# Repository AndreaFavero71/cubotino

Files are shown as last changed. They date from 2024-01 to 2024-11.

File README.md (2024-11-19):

# CUBOTino autonomous

This repo contains the relevant files for ....

How to make CUBOTino autonomous: A small, 3D printed, Rubik's cube solver robot
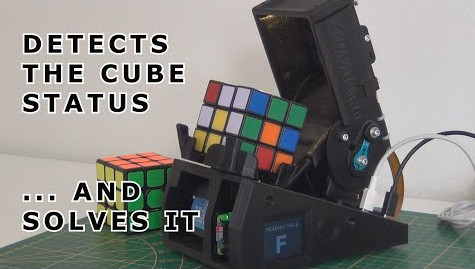
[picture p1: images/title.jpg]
title image


Further robot info at: https://www.instructables.com/CUBOTino-Autonomous-Small-3D-Printed-Rubiks-Cube-R/

An impression of the robot: https://youtu.be/dEOLhvVMcUg and https://youtu.be/YV-g_3STsBo

This is forked from the git repo made by heneault (thank you !!!), and updated to latest files versions.

This git repo simplifies the download of the individual files and automates as much a possible the deployment to the Raspberry Pi

This installation has proved to work on different Raspberry Pi models; Please report in case you experience issues.

# How to use it:
1. Flash your SD card according to the procedure in the [document here](doc/How_to_make_CUBOTino_autonomous_robot_20241119.pdf) , Chapter 7, Step1 to Step3
2. Put the sd card in the pi and power it. You can monitor the boot process if you connect an hdmi monitor to it but it is not essential. 
3. Try to connect to the Raspberry Pi via SSH. On Windows you can use Putty. On linux and mac you can type directly:
```
ssh pi@cubotino.local
```
4. If you can't reach the pi like this, you will have to scan your network to find the IP to use
5. After you are connected via ssh, type the following commands in the shell:
```
git clone https://github.com/AndreaFavero71/cubotino.git
cd cubotino/src
chmod +x install/setup.sh
sudo ./install/setup.sh
```
6. Make sure the script runs without error until the end. It should ask you to reboot. Type 'y' and hit enter.
7. If the question "Reboot (y/n)" does't appear, them the installation is facing issues; Try to fix the errors, and run the script again.
8. If the question "Reboot (y/n) does appear, You should get the proper environment after the reboot.

# Build the robot:
Follow the instructions (saved at /doc folder)

# Tuning the servos position via GUI (via VNC):
```
cd ~/cubotino/src
source .virtualenvs/bin/activate
python Cubotino_T_servos_GUI.py
```
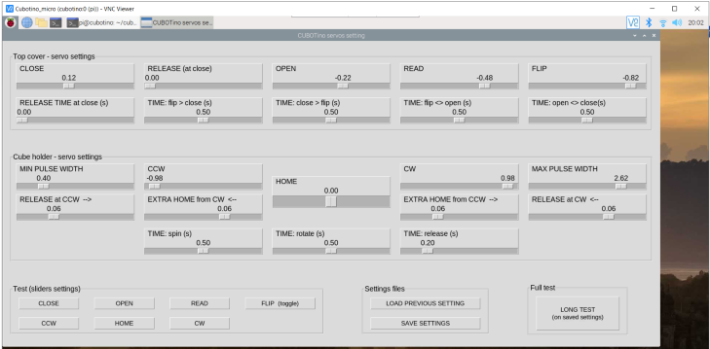
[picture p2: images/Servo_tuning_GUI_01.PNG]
title image


# Executing manually
From a shell, you can run the main python script like this:
```
cd ~/cubotino/src
source .virtualenvs/bin/activate
python Cubotino_T.py
```
of course, you can replace `Cubotino_T.py` by any other python scripts as mentioned in the documentation.

# Enabling autostart
When everything is tuned and you want to autostart the software automatically on reboot, just type :
```
    sudo crontab -e
```
select the nano editor '1' then go to the last line of the window and remove the first '#' character of the line . This uncomment the startup script that launches cubotino on startup. You can reboot after to test it.

# VNC connection
You can always connect with ssh. If you prefere VNC you can download the RealVNC client (this is the one I use). You just have that start it like this:
```
vncviewer cubotino.local
```
It will ask for the credential. Use 'pi' and the same password you use for ssh. You should have a desktop version in this way

Check out the "How_to_make ...  .pdf" document (at /doc folder) for further info.<br /><br />

# Please leave a feedback if you build it
I hope many of you will decide to build your own CUBOTino, and that you'll enjoy it as much much as I did. <br />
I hope you will also post an "I Made it", on the Instructables site of this project (link above); <br />
I can ensure you, seeing a new born CUBOTino makes me feel very well 🙂

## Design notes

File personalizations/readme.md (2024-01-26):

# Personalizations <br />

If you have personalized your Cubotino, and you'd like to share your cad files, SW snippets/file, etc: <br />

- This is the right folder. <br />
- Add a suffix with your name in front of all the files. <br />
- Add a text file, with your name in front :-) , to briefly explain what is about; If needed please add guidance for others. <br />
- Add a picture, with your name in front :-) , in case the personalization is mainly aesthetic. <br />
- Submit your pull request. <br />

Thank you <br />
Andrea <br />

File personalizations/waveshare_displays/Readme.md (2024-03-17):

# Waveshare 1.8 and 2 inch displays

- Both are fully compatable with the current version of cubotino.
- The [Waveshare 1.8inch](https://www.waveshare.com/product/displays/lcd-oled/lcd-oled-3/1.8inch-lcd-module.htm) display is a 160x128 ST7735 based display.
- The [Waveshare 2.0inch](https://www.waveshare.com/product/displays/lcd-oled/lcd-oled-3/2inch-lcd-module.htm) display is a 320x240 ST7789 based display.
- The STL files to print are attached for the USB-C Power input variants.
- The 1.8in display mounts to the PCB_Cover with 2.5mm screws, They are included with the screen
- The 2in display  mounts to the PCB_Cover with 2.0mm screws, They are included with the screen

# Wiring
- The connector on the back of the display is a [JST PH](https://www.jst.com/products/crimp-style-connectors-wire-to-board-type/ph-connector/) series connector.
- These displays come with a cable to connect the display to your PCB. Or they can be soldered. The cable provided has 
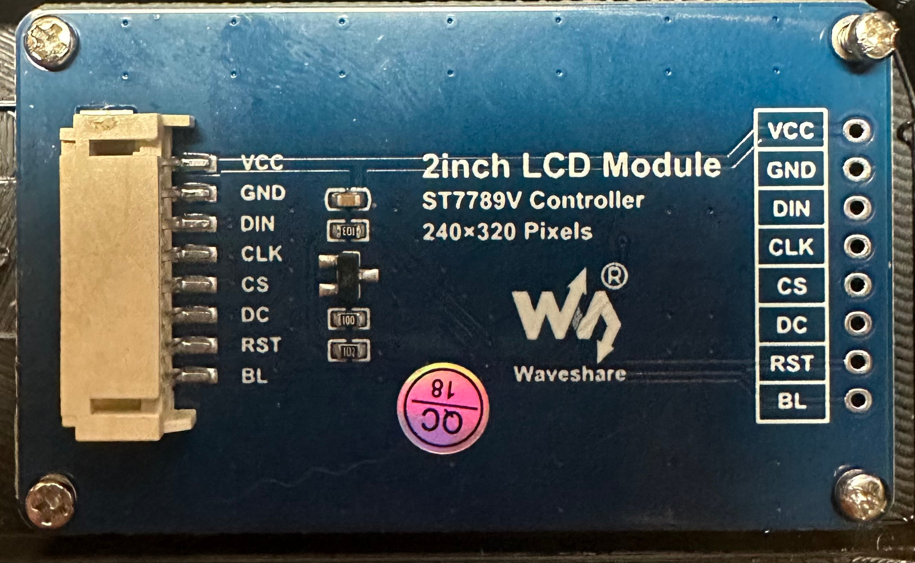
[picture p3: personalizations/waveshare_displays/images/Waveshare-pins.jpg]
Wire Diagram
individual leads with dupont connectors. 
- Using the [Cubotino Schematic](/connections_board/info/Schematic_Cubotino.pdf), the table below is used to connect the wires.

| Connections PCB Pin order | PCB Pin name | Waveshare Pin name | Waveshare Pin order |
|---|---|---|---|
| 1 | GND | GND | 2 |
| 2 | +3.3 | VCC | 1 |
| 3 | SCLK | CLK | 4 |
| 4 | MOSI | DIN | 3 |
| 5 | GP22 | RST | 7 |
| 6 | GP27 | DC | 6 |
| 7 | CS0 | CS | 5 |
| 8 | GP4 | BL | 8 |

# Assembly
- Here is a couple of pictures of my assembly.  Note: While I used a custom PCB. It is based on the [PCB Schematic](/connections_board/info/Schematic_Cubotino.pdf) in this project.
- There is about 20mm between the connections pCP and the Display.
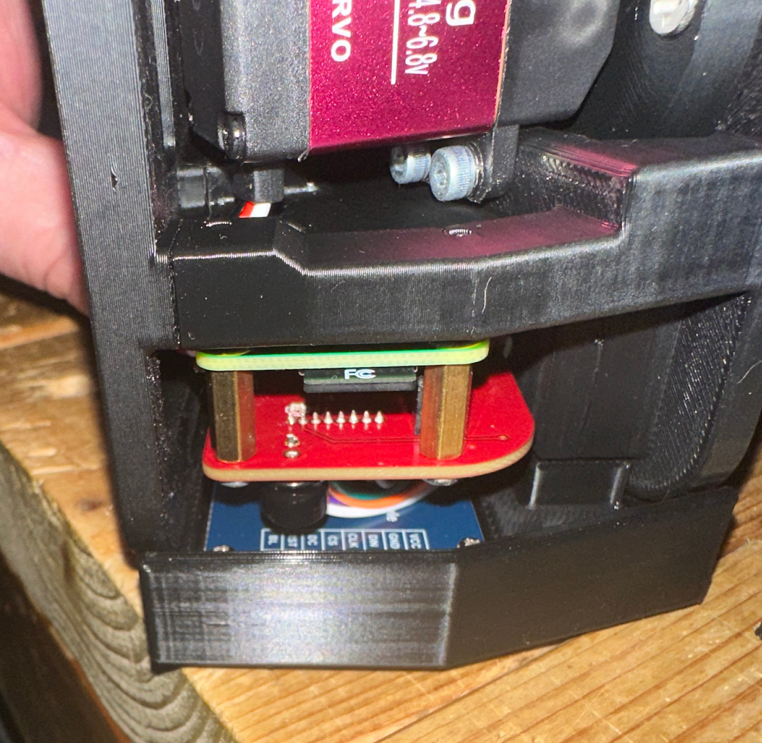
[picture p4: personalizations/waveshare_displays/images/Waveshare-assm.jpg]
Assembly

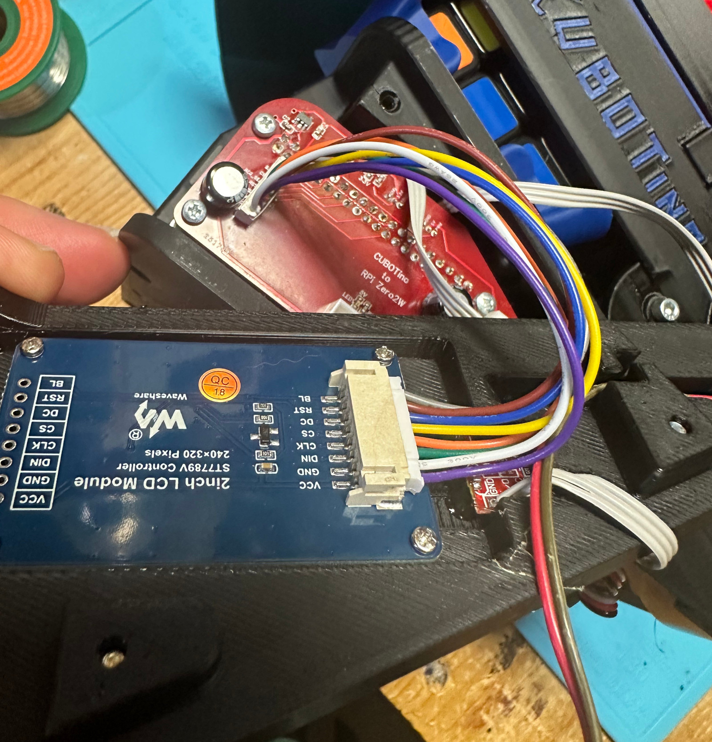
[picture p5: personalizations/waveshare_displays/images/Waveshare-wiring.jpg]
Wiring


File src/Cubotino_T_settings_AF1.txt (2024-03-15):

{
"frameless_cube": "auto",
"disp_type": "st7735",
"disp_width": "130",
"disp_height": "162",
"disp_offsetL": "-2",
"disp_offsetT": "-2",
"disp_flip": "false",
"camera_width_res": "640",
"camera_hight_res": "480",
"s_mode": "7",
"kl": "0.95",
"x_l": "70",
"x_r": "60",
"y_u": "20",
"y_b": "95",
"warp_fraction": "7",
"warp_slicing": "1.5",
"square_ratio": "1",
"rhombus_ratio": "0.3",
"delta_area_limit": "0.7",
"sv_max_moves": "20",
"sv_max_time": "2",
"collage_w": "1024",
"marg_coef": "0.06",
"cam_led_bright": "0.1",
"detect_timeout": "40",
"show_time": "7",
"warn_time": "1.5",
"quit_time": "3.5",
"cover_self_close": "true",
"vnc_delay": "0.0",
"built_by": "",
"built_by_x": "25",
"built_by_fs": "16",
"fcs_delay": "3"
}

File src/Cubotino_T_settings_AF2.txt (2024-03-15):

{
"frameless_cube": "auto",
"disp_type": "st7735",
"disp_width": "128",
"disp_height": "164",
"disp_offsetL": "0",
"disp_offsetT": "-4",
"disp_flip": "false",
"camera_width_res": "640",
"camera_hight_res": "480",
"s_mode": "7",
"kl": "0.95",
"x_l": "56",
"x_r": "106",
"y_u": "48",
"y_b": "100",
"warp_fraction": "7.2",
"warp_slicing": "1.5",
"square_ratio": "1.0",
"rhombus_ratio": "0.3",
"delta_area_limit": "0.7",
"sv_max_moves": "20",
"sv_max_time": "2.0",
"collage_w": "1024",
"marg_coef": "0.06",
"cam_led_bright": "0.04",
"detect_timeout": "40",
"show_time": "7",
"warn_time": "1.5",
"quit_time": "3.5",
"cover_self_close": "True",
"vnc_delay": "0.5",
"built_by": "",
"built_by_x": "25",
"built_by_fs": "16",
"expo_shift": "-0.2",
"fcs_delay": "3.0"
}

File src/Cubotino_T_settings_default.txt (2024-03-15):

{
"frameless_cube": "false",
"disp_type": "st7735",
"disp_width": "128",
"disp_height": "160",
"disp_offsetL": "0",
"disp_offsetT": "0",
"disp_flip": "false",
"camera_width_res": "640",
"camera_hight_res": "480",
"s_mode": "7",
"kl": "0.95",
"x_l": "0",
"x_r": "0",
"y_u": "0",
"y_b": "0",
"warp_fraction": "7",
"warp_slicing": "1.5",
"square_ratio": "1",
"rhombus_ratio": "0.3",
"delta_area_limit": "0.7",
"sv_max_moves": "20",
"sv_max_time": "2",
"collage_w": "1024",
"marg_coef": "0.1",
"cam_led_bright": "0.1",
"detect_timeout": "40",
"show_time": "7",
"warn_time": "1.5",
"quit_time": "3.5",
"cover_self_close": "false",
"vnc_delay": "0.0",
"built_by": "",
"built_by_x": "25",
"built_by_fs": "16",
"expo_shift": "-0.6",
"fcs_delay": "3"
}

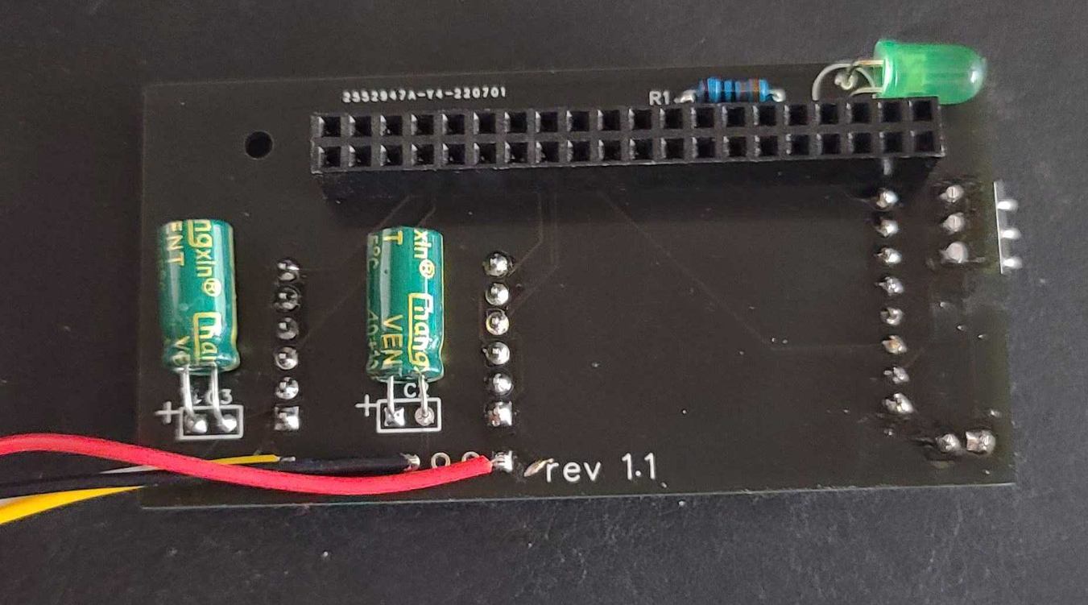
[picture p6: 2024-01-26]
connections_board/info/Cubotino_Rev_1.1_Back_View.jpg

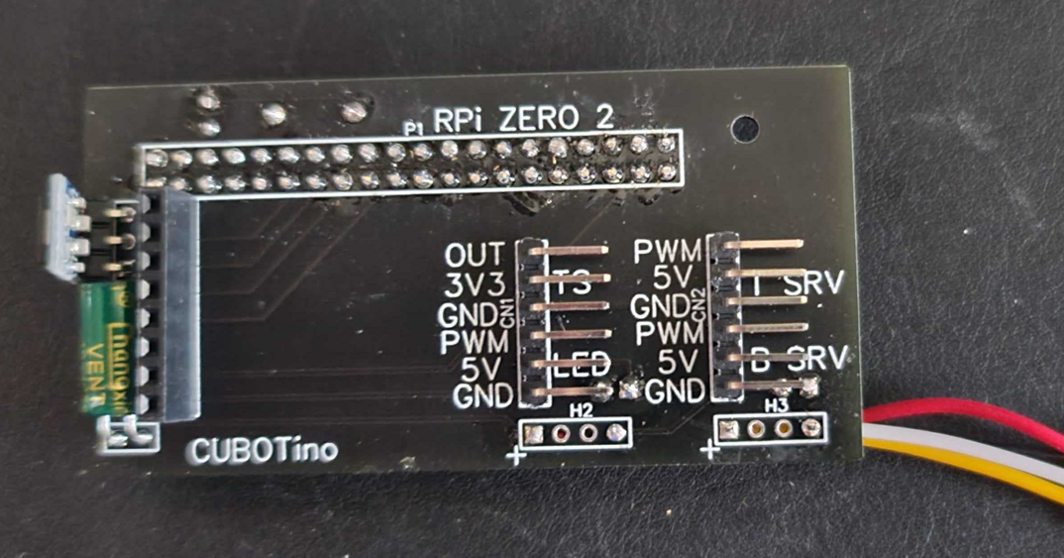
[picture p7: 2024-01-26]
connections_board/info/Cubotino_Rev_1.1_Front_View.jpg

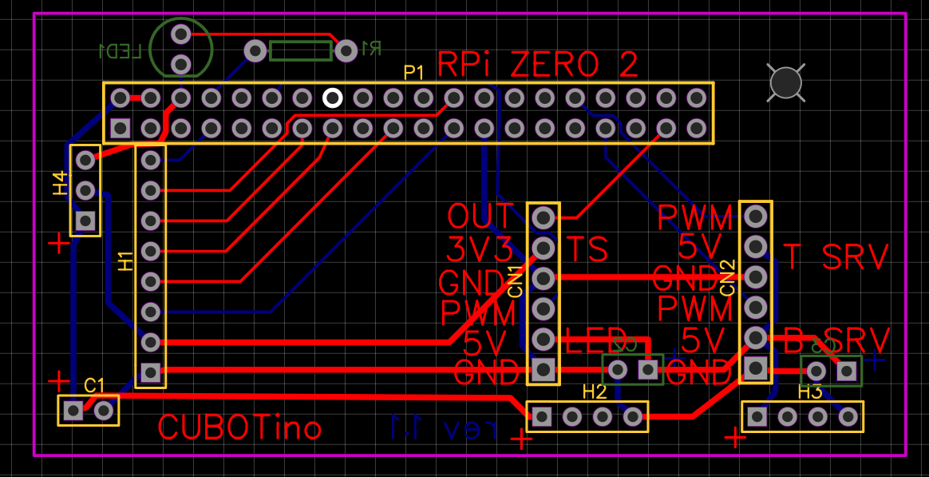
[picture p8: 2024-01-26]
connections_board/info/Cubotino_PCB_Rev-1.1.png

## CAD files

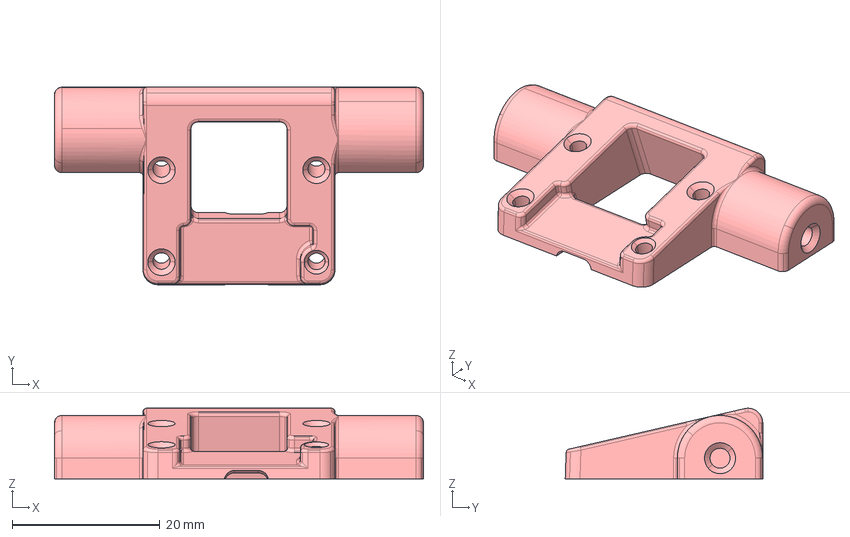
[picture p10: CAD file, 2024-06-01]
stp/PiCamera_holder_V1_V2_V3.stp
50.0 x 26.8 x 9.57 mm

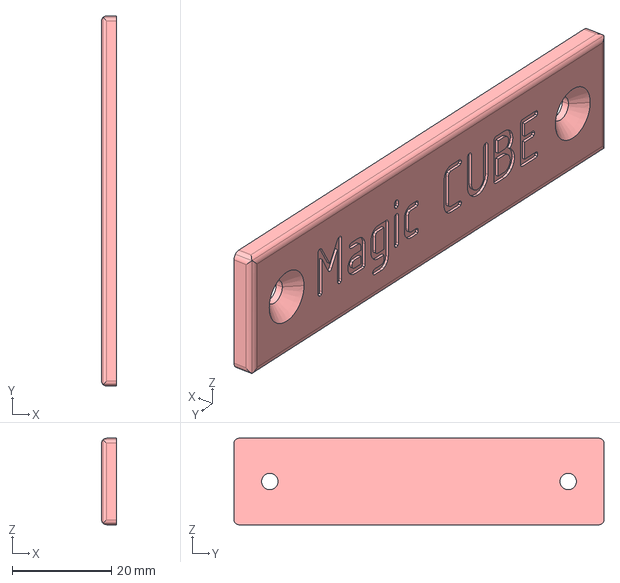
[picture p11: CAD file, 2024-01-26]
stp/Personaliz_plate_01.stp
3.00 x 74.4 x 17.4 mm

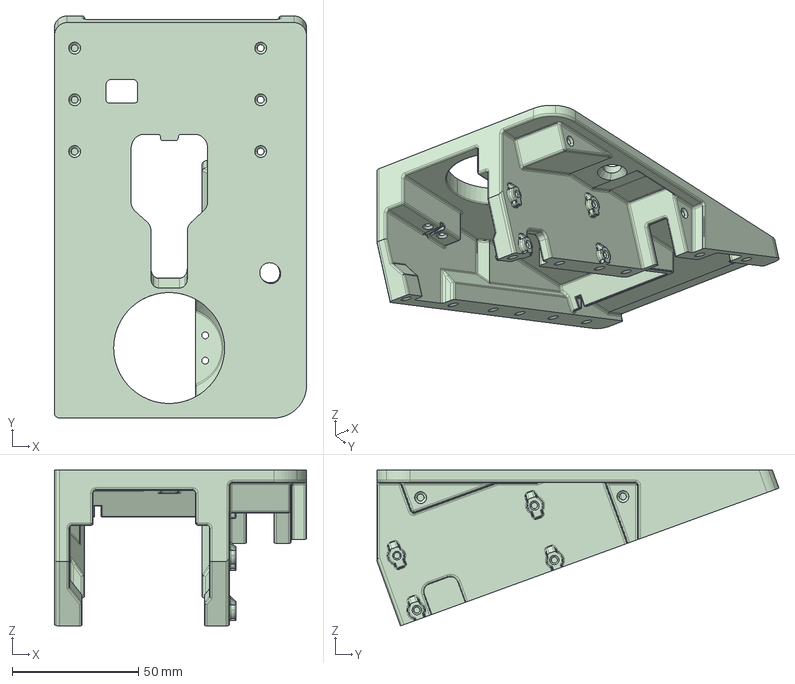
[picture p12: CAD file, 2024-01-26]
stp/Structure.stp
100.0 x 159.4 x 61.8 mm

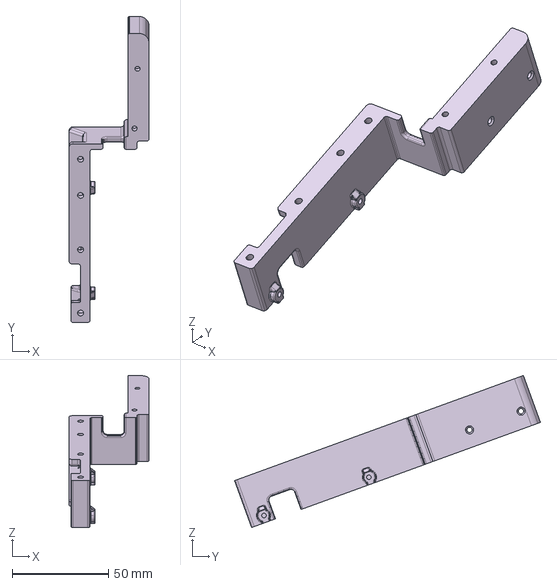
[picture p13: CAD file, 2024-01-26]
stp/Extension_middle.stp
41.5 x 158.9 x 79.0 mm

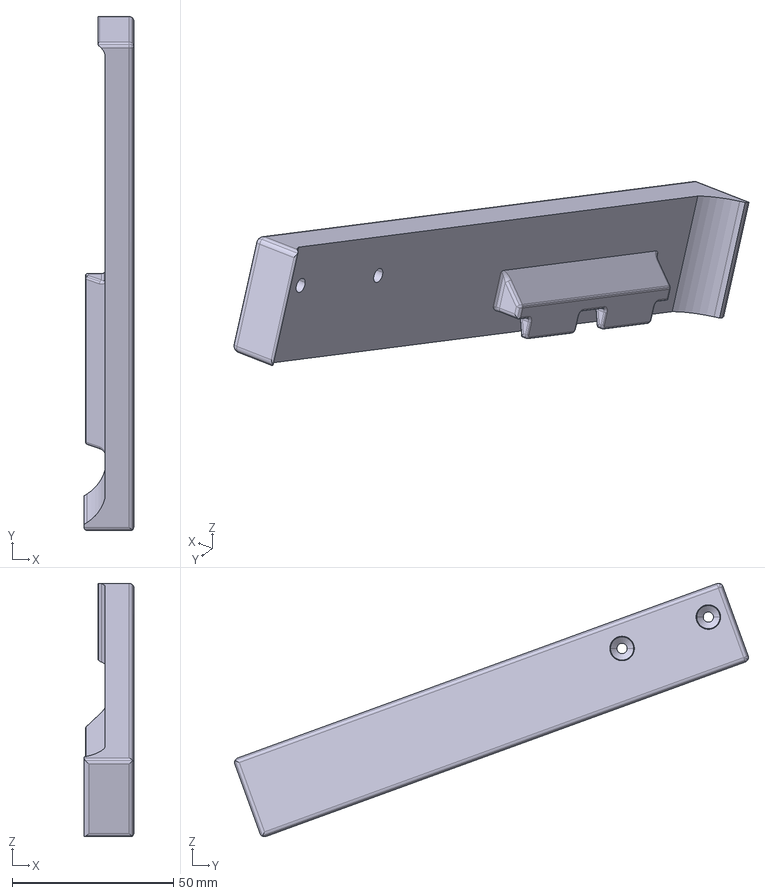
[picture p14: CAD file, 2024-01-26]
stp/Extension_right.stp
15.5 x 159.3 x 78.5 mm

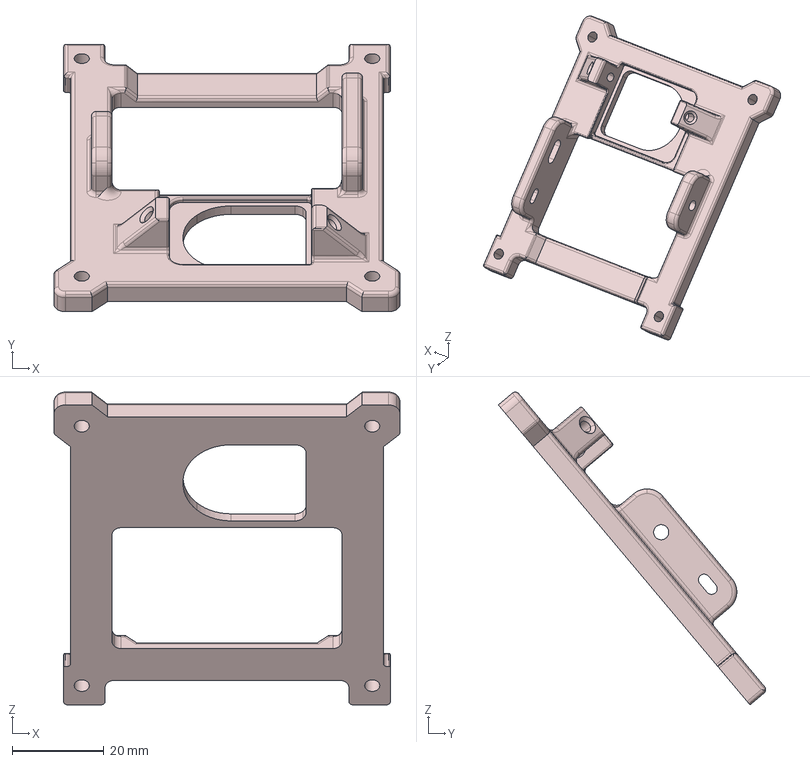
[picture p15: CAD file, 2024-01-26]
stp/Picamera_holder_frame.stp
75.5 x 58.4 x 68.3 mm

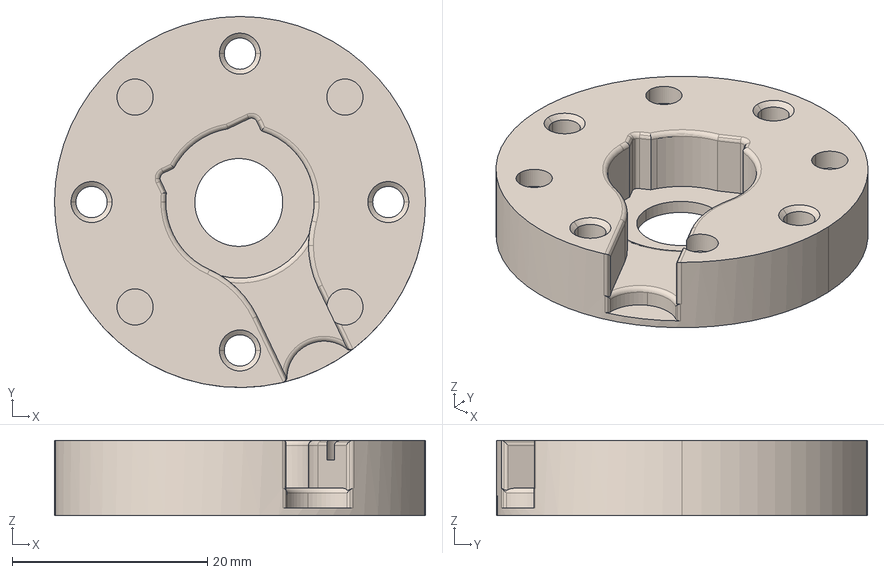
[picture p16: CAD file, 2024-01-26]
stp/Alternative_Servo_axis_inf.stp
38.0 x 38.0 x 7.70 mm

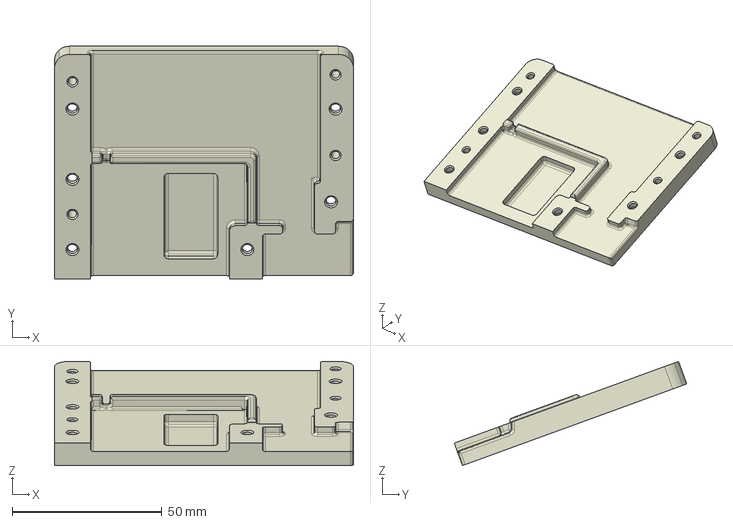
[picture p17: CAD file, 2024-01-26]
stp/Baseplate_rear.stp
100.0 x 77.8 x 34.8 mm

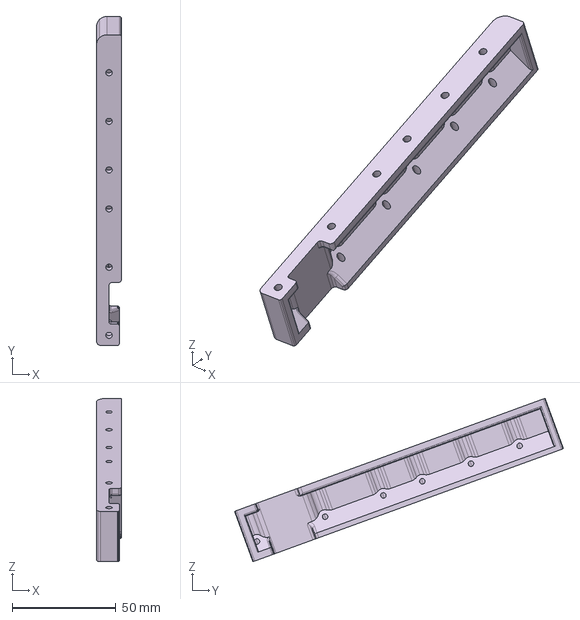
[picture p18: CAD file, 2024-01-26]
stp/Extension_left.stp
12.0 x 158.9 x 79.0 mm

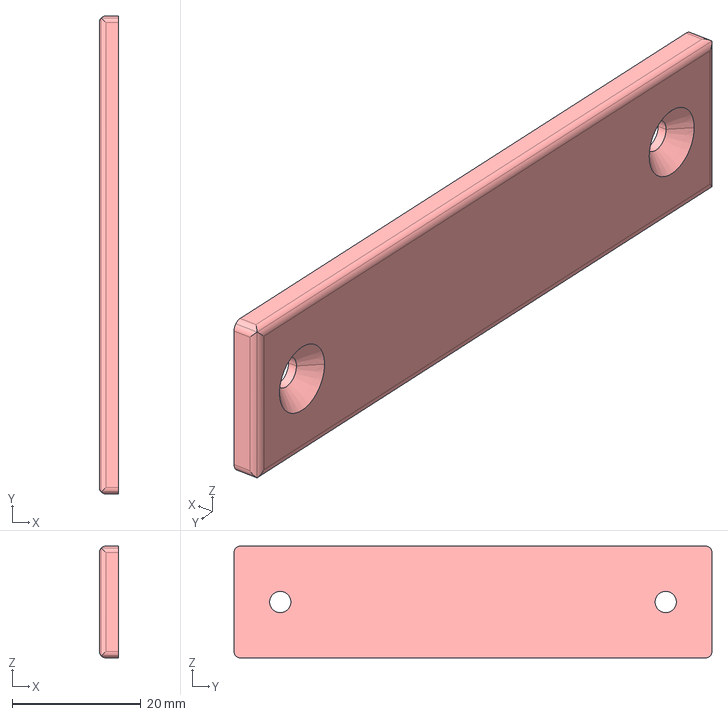
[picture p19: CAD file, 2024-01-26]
stp/Personaliz_plate.stp
3.00 x 74.4 x 17.4 mm

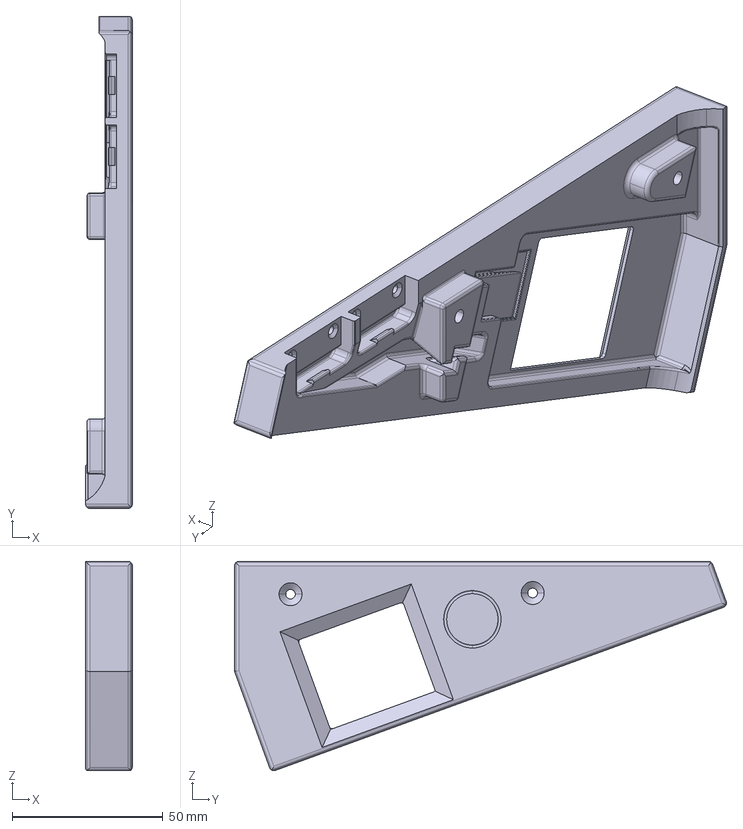
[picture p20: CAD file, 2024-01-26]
stp/PCB_cover_display.stp
15.5 x 163.0 x 69.4 mm

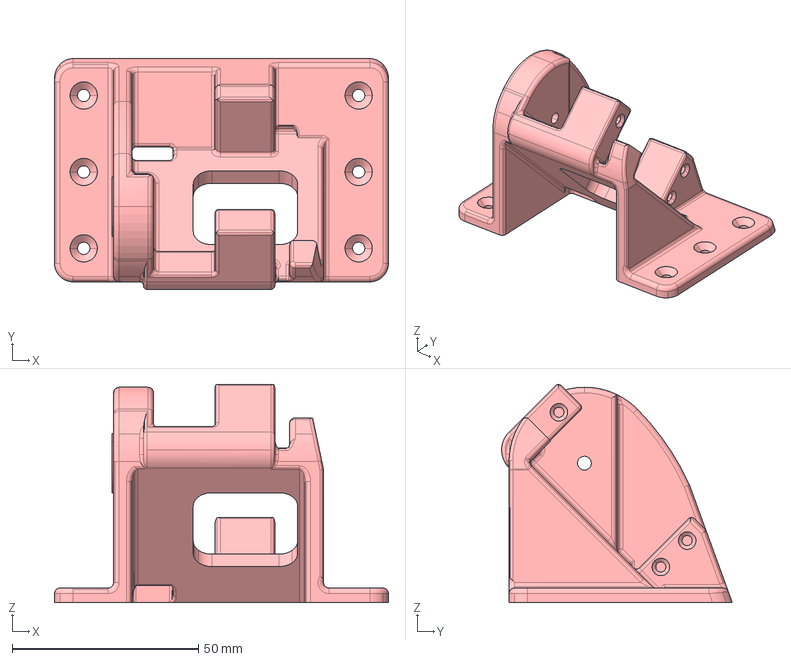
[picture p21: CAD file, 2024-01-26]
stp/Hinge.stp
89.6 x 61.9 x 58.6 mm

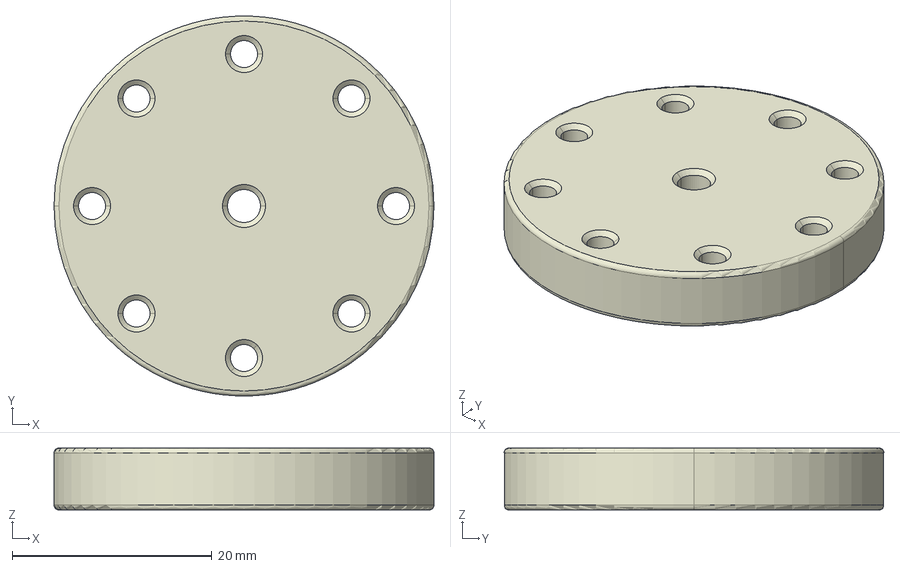
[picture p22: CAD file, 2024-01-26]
stp/Alternative_Servo_axis_sup.stp
38.0 x 38.0 x 6.20 mm

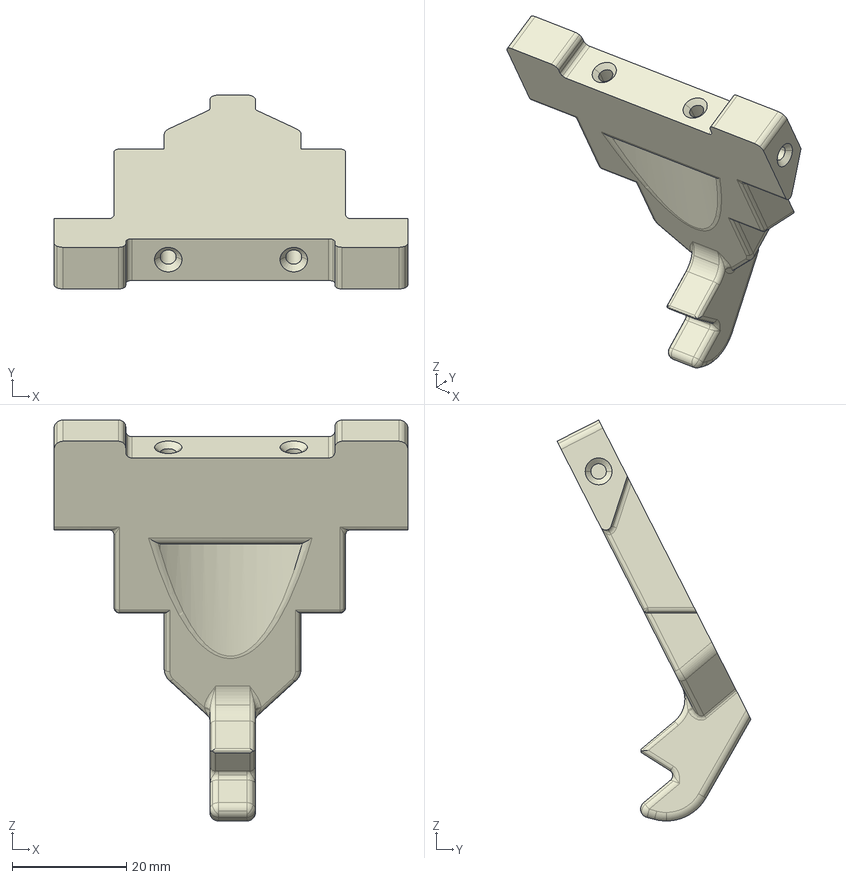
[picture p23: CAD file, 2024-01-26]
stp/Lifter.stp
62.0 x 34.0 x 70.3 mm

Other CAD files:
stp/Servo_axis_inf.stp
stp/Baseplate_front.stp
stp/Servo_axis_sup.stp
stp/Top_cover.stp
stl/Alternative_Servo_axis_inf.stl
stl/Alternative_Servo_axis_sup.stl
stl/Baseplate_rear.stl
stl/Extension_left.stl
stl/Extension_middle.stl
stl/Extension_right.stl
stl/Lifter.stl
stl/Personaliz_plate.stl
stl/Personaliz_plate_01.stl
stl/PiCamera_holder_V1_V2_V3.stl
stl/Servo_axis_inf.stl
stl/Servo_axis_sup.stl
stp/PCB_cover_display_UsbC.stp

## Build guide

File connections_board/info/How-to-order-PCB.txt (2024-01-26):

How to Order PCB

Please refer to:
https://docs.easyeda.com/en/PCB/Order-PCB

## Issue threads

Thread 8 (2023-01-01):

Schematic for the PCB

belenhed, 2023-01-01:
Hello can we have the schematic for the PCB so maybe we can make one at home with a CNC?
Thanks

AndreaFavero71, 2023-10-15:
This answer is absolutely late.....anyhow:
https://github.com/AndreaFavero71/cubotino/blob/main/connections_board/info/Schematic_Cubotino.pdf

AndreaFavero71, 2023-10-15:
Schematic is finally loaded

Closed 2023-10-15.

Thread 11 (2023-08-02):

Errors in RPi setup

MasterMD, 2023-08-02:
Hi!
Great project !!
During the execution of the setup.sh I got an error :
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
but the procedure continues.
But at about 47% of the unpacking it stops with this error:
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
I repeated the whole procedure (from writing new image on the SD card), but same result.
What to do?

kind regards,
Maarten

AndreaFavero71, 2023-08-06:
Hi, I'm going to be holiday for one more week and I'm not equipped to run any test.
In case there are recent changes on libraries, blocking the installation, there is little I can do shortly.

What I can do now, is to double check with you if any error at your side.
On 15th July 2023 the installation process was working fine: If you share your email address I'll send you the printout log I've saved (and downloaded from my NAS).
Are you sure the flashed OS is the "Raspberry Pi OS (Legacy)”, not the default one proposed by the Raspberry Pi Imager?
If the chosen OS is correct, which Raspberry Pi board are you using?

Kind regards
Andrea

MasterMD, 2023-08-06:
Hi Andrea,

Thanks for your response!

After my experience with the RPi installation part, I was a little confused what to do.
(burning the image and verifying had been succesfull)

A few days later I decided to try it again with a different SD card, and ... the procedure finished succesfull !!
Sorry, that I didn't update my GitHub thread yet ...

I went on with the assembly, and 'discovered' that my camera extension flat cable was of a wrong type
(some years ago I build a cube resolver with RPi 3 and Technic Lego construction, so I thought I have a camera and cable ;-)
but I wasn't aware that the Zero has a different connection).

I ordered a new cable, and started testing. Unfortunately the camera didn't function (at all).
The connection at the Pi Zero appears to be rather fragile, but after re-arranging the camera still doesn't work.
Now I am awaiting a new camera board; hopely I can proceed then.

I admire the way you have set-up this whole project: the lovely design, and surely the extended documentation.
I found some details to (maybe) improve. I you like it, I will send them as soon as I have my Cubotino operating.

Thanks again !

Kind regards,
Maarten

AndreaFavero71, 2023-08-06:
Hi Maarten, very good you found the solution for the setup issue.
I'll close this thread with a comment about microSD and possible setup
errors, and I'll add it to the troubleshooting chapter.

I received once a bad camera cable: At the CSI connector extremity, the
insulation was too large at one side (and narrow al the opposite side)
preventing the traces alignment (connection) to the CSI connector.
I did cut away a narrow strip of insulation, and inserted the cable forced
to that side: That arrangement is still working after one year, including a
few reopening of it.

I'm always open for corrections and improvements; Please collect and share
them via email, to ***@***.***, once you'll have your bot up
and running.

Kind regards
Andrea

Il dom 6 ago 2023, 12:16 MasterMD ***@***.***> ha scritto:

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

AndreaFavero71, 2023-08-14:
In case of Errors in Rpi setup, try with a different microSD as it might be the source of the problem

Closed 2023-08-14.

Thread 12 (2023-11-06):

CPL file for JLCPCB board assembly

KH6JAG, 2023-11-06:
Is there a CPL file available to request a quote from JLCPCB for board and assembly?
The link given in connections_board/info/ is only for the board.

When chatting with JLCPCB today, I was advised that I need to either provide the CPL file or do a complete design using EadyEDA.
The Gerber files imported without error to do a board order, but they cannot be imported into Easy EDA.

I've also asked PCBWAY for a quote on the assembled board - they usually respond in 2-3 days with a quote for assembled boards.

Thanks for all your Cubotino project efforts!

AndreaFavero71, 2023-11-06:
Hi, I just googled what CPL file is meant for, and it looks like it includes the BOM (all compoents), as per the issue title you have raised :-)
I'm afraid I don't have the CPL file, the board has been drawn by another Maker and the files I received are those that are published.
I hope you'll take a big breath, and decide to order/solder the components by yourself...
Regards, Andrea

KH6JAG, 2023-11-07:
<!--
/* Font Definitions */
@font-face
	{font-family:"Cambria Math";
	panose-1:2 4 5 3 5 4 6 3 2 4;}
@font-face
	{font-family:Calibri;
	panose-1:2 15 5 2 2 2 4 3 2 4;}
@font-face
	{font-family:"Malgun Gothic";
	panose-1:2 11 5 3 2 0 0 2 0 4;}
@font-face
	***@***.*** Gothic";}
/* Style Definitions */
p.MsoNormal, li.MsoNormal, div.MsoNormal
	{margin:0in;
	font-size:11.0pt;
	font-family:"Calibri",sans-serif;}
a:link, span.MsoHyperlink
	{mso-style-priority:99;
	color:blue;
	text-decoration:underline;}
.MsoChpDefault
	{mso-style-type:export-only;}
@page WordSection1
	{size:8.5in 11.0in;
	margin:1.0in 1.0in 1.0in 1.0in;}
div.WordSection1
	{page:WordSection1;}
-->Thanks for the reply.  I think I can build the CPL file from the info provided by the board maker on the PCBWAY share site.The JLCPCB site offered a potential lower cost source of supplyI have already have soldered a breadboard unit from the Instructable.The newer build is to support a group of youngsters so they wouldn’t need to solder as in requires SMD and just do a mechanical build.Thanks again,  Jim Sent from Mail for Windows From: AndreaSent: Monday, November 6, 2023 1:37 PMTo: AndreaFavero71/cubotinoCc: KH6JAG; AuthorSubject: Re: [AndreaFavero71/cubotino] CPL file for JLCPCB board assembly (Issue #12) Hi, I just googled what CPL file is meant for, and it looks like it includes the BOM (all compoents), as per the issue title you have raised :-)I'm afraid I don't have the CPL file, the board has been drawn by another Maker and the files I received are those that are published.I hope you'll take a big breath, and decide to order/solder the components by yourself...Regards, Andrea—Reply to this email directly, view it on GitHub, or unsubscribe.You are receiving this because you authored the thread.Message ID: ***@***.***> 

AndreaFavero71, 2023-11-08:
Hi Jim,
I've the feeling you are referring to the the board designed by G2G, as you're mentioning smd components.
This board, despite having some positive aspects, is not supported by me and not described in the instructions. In my opinion, this board increases complexity by adding extra connectors (i.e on the display) and smd components.
If you prefer this board, as it comes fully assembled, please note you'll have to use specific connectors at the servos, led module,  touch sensor and display: For reference, please check the "I MADE IT" made by g2maurer at Instructables (https://www.instructables.com/CUBOTino-Autonomous-Small-3D-Printed-Rubiks-Cube-R/#discuss).
g2maurer has posted the email in case there are maker interested on getting that board: Please check the chat at Instructables page for his/her email address.
You'll also notice the display is screwed directly to the PCB_cover, therefore you'll better ask g2maurer for the stl file.

For the supported board (V1.6) the gerber files are saved at /gerber folder on this project; This board is "just" essential, no BOM saved at the boards manufacturer, yet it only uses little through hole components.
This board is the one described in the instructions.

I'm ok with both option, yet it's important you're aware about the differences.
I hope you and the youngsters will have fun with the project.
Regards, Andrea

AndreaFavero71, 2023-11-11:
This issue relates to a board version that isn't supported by Andrea Favero, board not covered in the instructions.
The supported board (V1.6) doesn't have smd components, neither the CPL file yet is is simple to solder at home.

KH6JAG, 2023-11-11:
Thank you for the reply.  We have a project that is building as many of the Rubik's robots that have good documentation.  Cubotino has one of the best documentation sets.  I was able to get a build quote for the boards that required the CPL file.  I'll send you an update once the units are built with these boards.

Closed 2023-11-11.

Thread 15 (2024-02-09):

Display test not working and install doesnt work properly.

varkanoid, 2024-02-09:
Hi,

I decided to change my microsd card before I ran through the setup process and tuning. I also saw you had updated recently so I thought I will refresh the whole thing. I had only done a few things before like test the display was working with your test script which it was. I started from scratch and imaged the new micro sd. I then cloned your repository and followed your install instructions.

Issue 1 was when you click y to restart, you get no GUI after the restart. I had to enable it myself with raspi-config.
Issue 2 now when I run the display test I get these errors below. This is strange because with the previous install it worked fine.

(.virtualenvs) pi@cubotino:~/cubotino/src $ python Cubotino_T_display.py
Activated pigpiod
Error on converting imported parameters to int
Display test for 20 seconds
Display shows rectangles, text and Cubotino logo
Traceback (most recent call last):
  File "/home/pi/cubotino/src/Cubotino_T_display.py", line 298, in <module>
    display.test1_display()
  File "/home/pi/cubotino/src/Cubotino_T_display.py", line 217, in test1_display
    w = self.disp_w                                            # display width, retrieved by display setting
AttributeError: 'Display' object has no attribute 'disp_w'

So I am using the one dated 22nd January 2024.

Any ideas ?

varkanoid, 2024-02-09:
Also getting this error when I try to run the Tuning GUI.
(.virtualenvs) pi@cubotino:~/cubotino/src $ python Cubotino_T_servos_GUI.py

Activated pigpiod
Error on converting imported parameters to int
Traceback (most recent call last):
  File "/home/pi/cubotino/src/Cubotino_T_servos_GUI.py", line 30, in <module>
    import Cubotino_T_servos as servo    # custom library controlling Cubotino servos and led module
  File "/home/pi/cubotino/src/Cubotino_T_servos.py", line 37, in <module>
    s_disp.set_backlight(0)     # display backlight is set off
  File "/home/pi/cubotino/src/Cubotino_T_display.py", line 85, in set_backlight
    self.disp.set_backlight(value)
AttributeError: 'Display' object has no attribute 'disp'

varkanoid, 2024-02-09:
Seems some kind of issue with setting the display ?

(.virtualenvs) pi@cubotino:~/cubotino/src $ python Cubotino_T_servos.py -set 0

Activated pigpiod
Error on converting imported parameters to int
Traceback (most recent call last):
  File "/home/pi/cubotino/src/Cubotino_T_servos.py", line 37, in <module>
    s_disp.set_backlight(0)     # display backlight is set off
  File "/home/pi/cubotino/src/Cubotino_T_display.py", line 85, in set_backlight
    self.disp.set_backlight(value)
AttributeError: 'Display' object has no attribute 'disp'

AndreaFavero71, 2024-02-09:
Hi varkanoid,
you are right, I copied the wrong Cubotino_T_settings.txt file.
The settings from this file are uploaded by different scripts.
I have set a system from flashing the image onward: It looks ok now.
Please feedback if it works at your end too.
Regards, Andrea

varkanoid, 2024-02-09:
Works again now than you very much it is appreciated. :)

Just a small thing you left the displ width at 130 instead of the default 128. I know you changed it to 130 for your screen but it works fine with 128 with my screen. Just a minor thing you should be aware of.

AndreaFavero71, 2024-02-09:
Hi, thank you for the note ... just checked that 130 is into the file and instruction since June 2022. I'm going to correct the file now, and the instruction for the next revision.
Wrt the 1st issue you pointed out, after the installation, the Desktop environment can be activated by editing crontab: This is the way I've indicated in the instructions, dor sure there are other ways.
I'm going to close this Issue.
Enjoy the project, Andrea

Closed 2024-02-09.

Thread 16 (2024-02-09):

Error when Cubotino_T_coordinates.txt is missing (or empty)

varkanoid, 2024-02-09:
Hi,

sorry found another issue.

I have done my tuning succesfully. Came to start the solver and it errors below

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

varkanoid, 2024-02-09:
Seems to be this bit in the file it fails on as the .txt file doesnt exist it doesnt define the lines parameter.
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

varkanoid, 2024-02-09:
So I added a blank Cubotino_T_coordinates.txt file and it passed that section with an error.
However I now get this error.
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

AndreaFavero71, 2024-02-10:
Hi Varkanoid, you're right again.
Released an improved version.
Regards, Andrea

varkanoid, 2024-02-10:
Thanks its working now.

varkanoid, 2024-02-10:
Working once again great job. Solved my first cube :)

Closed 2024-02-10.

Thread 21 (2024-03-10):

servos_setting_GUI.py file is required?

AgnesBarta, 2024-03-10:
Hi,

This project sounds really great, we are trying to bring up the source code. We have some issue to init the GUI to do the fine tuning setup. When we are running Cubotino_T_servos_GUI.py it is expecting DISPLAY env variable to be set what is not the case for us. In the latest documentation we see to bring up the GUI with servos_setting_GUI.py but that one I am not able to see in the repo. Could you please help us if we miss something? Thank you so much.

AndreaFavero71, 2024-03-10:
Hi, the GUI file is named Cubotino_T_servos_GUI.py and it requires the virtual environment.
Anyhow, please be informed that today I have released a rather large update (V7.0), involving 7 python files and 2 text files.
Please check, and report, the version of the Cubotino_T.py (add the argument -v , again after activating the virtual enviroment) that gives you the problem.

AgnesBarta, 2024-03-10:
Thank you for confirming. Finally we got the issue resolved and were able to bring the GUI app. Thank you for the quick answer.

AndreaFavero71, 2024-03-10:
Very good. Still applies that I have released an update today, and you might benefit from starting with it.
If of your interest, below the necessary command:
```
git reset --hard origin/main
git pull
```

Closed 2024-03-11.

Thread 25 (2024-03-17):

Settings files getting corrupted when saving from GUI

paul-1, 2024-03-17:
I'm using the GUI to tune my servos.  When saving from the GUI, I'm seeing values getting written wrong, and sometimes after writing, the file is no longer able to be read, as the json has a corrupt format.  I believe it is because of conflicting open calls like this.

https://github.com/AndreaFavero71/cubotino/blob/e5fcf2e7af7ece9f6fb719ae576c74a5f2e58baa/src/Cubotino_T_settings_manager.py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

This is mixing python native file operations with low level os file routines.  I'm not even sure how its working, but they are not compatible.  I would recommend you just use the python open() commands.  Those work with the context manager that you are using.

AndreaFavero71, 2024-03-18:
Hi Paul, I need to check for this.
I've never had problem with this approach. Differently, I had rights issue at the time those two files were cloned from the remote repository, and the robot attempting to write on those.

paul-1, 2024-03-18:
It does not happen every time.  It feels like there are multiple writes to the same file going on.  One common result is the closing } getting repeated twice.   I also saw values that were in the GUI as 3.1 getting written as “3”

Sent from my iPhone

On Mar 18, 2024, at 1:30 PM, Andrea ***@***.***> wrote:

Hi Paul, I need to check for this.
I've never had problem with this approach. Differently, I had rights issue at the time those two files were cloned from the remote repository, and the robot attempting to write on those.

—
Reply to this email directly, view it on GitHub<https://github.com/AndreaFavero71/cubotino/issues/25#issuecomment-2004529060>, or unsubscribe<https://github.com/notifications/unsubscribe-auth/ABRMN4LEKLBGYVCZCHKDBN3YY4QELAVCNFSM6AAAAABE2NAHXKVHI2DSMVQWIX3LMV43OSLTON2WKQ3PNVWWK3TUHMZDAMBUGUZDSMBWGA>.
You are receiving this because you authored the thread.Message ID: ***@***.***>

AndreaFavero71, 2024-03-18:
Ah, then I know: It happens when writing on the same file with less characters than the initial file: The old } remains right after the new inserted one.

After each
```
f.write(json.dumps(whaterver_filename, indent=0))
```
Please add
```
f.truncate()
```
I'll test at my side, please give it a test at yours :-)

AndreaFavero71, 2024-03-18:
Hi Paul,
the settings are saved in the Json files as string
The settings reppresenting values are converted, to integers or to floats, when imported by the Cubotino_T_settings.manager.py
In don't have an explanation about value 3.1 at GUI and "3" at the Json file, but the other way around is possible: Most of the sliders have steps larger than 0.01 (i.e. 0.02) while some default settings are for instance at 0.33 (legacy from before the GUI time).

For the issue you have raise, double } }, it can be reproduced sistematically:
- Set HOME to 0.12 and save. The Json file ends with one }
- Set HOME to 0.0 and save. The Json file ends with two }, as this time less characters were saved while some old ones remained at the file end.

I'm going to commit a fix.

paul-1, 2024-03-18:
Okay, the update seems to fix the bad json, so now the files are getting written properly.  I should could not remember which slider was wrong when I responded today (I was at work)

But the error is in 'warp_slicing' and the problem is reading the slider as an int.
https://github.com/AndreaFavero71/cubotino/blob/bce2f8f3f826e9d64b74439d2aa6d9244493a5a6/src/Cubotino_T_servos_GUI.py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

AndreaFavero71, 2024-03-19:
Hi paul, you're sharp and right.
The warp_slicing parameter is meant to be a float while the slider in takes as integer; This mistake is there since day one of the GUI, 18th April 2023.
This error isn't critic, I'll push the correction once something else will require a commit.

AndreaFavero71, 2024-04-01:
Correction is applied b01a6ec56089ce0dfbc9d7d62913982ef89324f2

Closed 2024-04-01.

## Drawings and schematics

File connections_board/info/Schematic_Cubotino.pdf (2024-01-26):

## USB-C RECEPTABLE

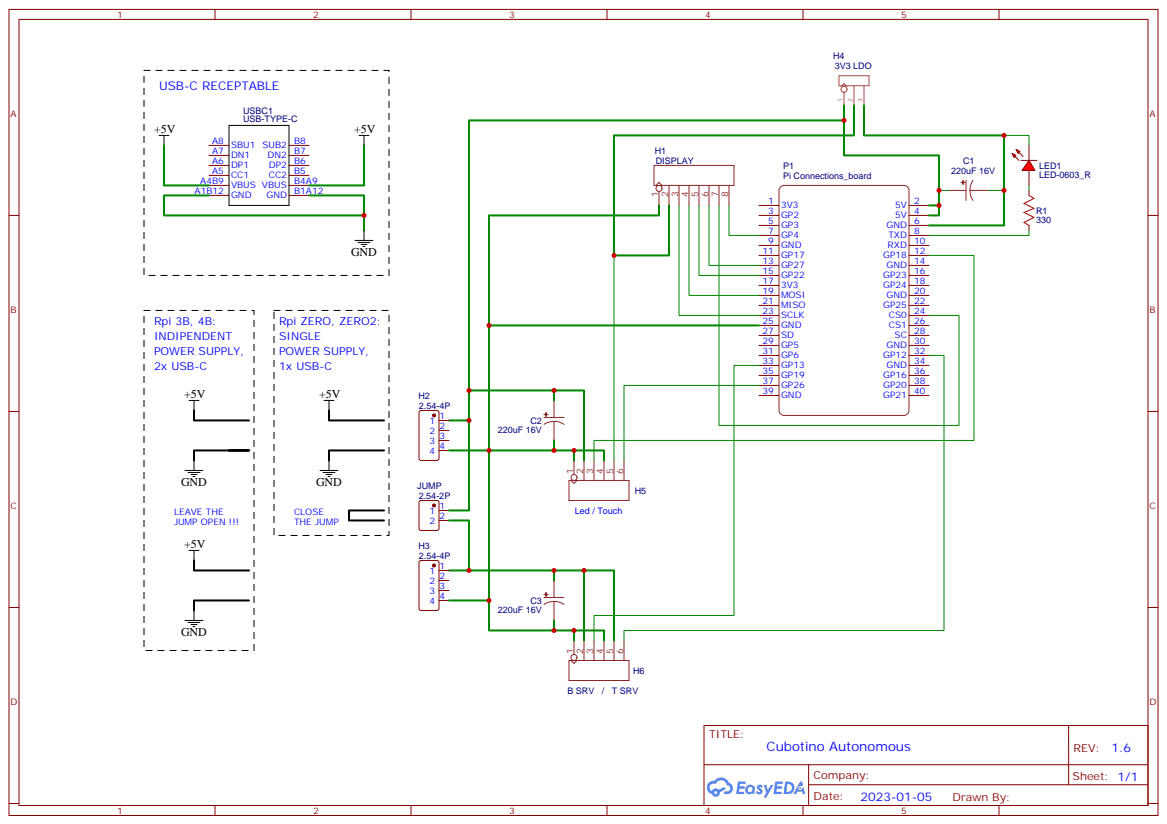
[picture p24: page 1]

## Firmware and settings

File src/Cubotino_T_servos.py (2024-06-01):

#!/usr/bin/python
# coding: utf-8

"""
#############################################################################################################
# Andrea Favero 31 May 2024
#
# This script relates to CUBOTino Autonomous, a very small and simple Rubik's cube solver robot 3D printed
# CUBOTino autonomous is the 'Top version', of the CUBOTino versions
# This specific script controls two servos based on the movements string from Cubotino.py
# 
# Possible moves with this robot
# 1) Spins the complete cube ("S") laying on the bottom face: 1 means CW 90deg turns, while 3 means 90CCW turn
# 2) Flips the complete cube ("F") by "moving" the Front face to Bottom face: Only positive values are possible
# 3) Rotates the bottom layer ("R") while costraining the 2nd and 3rd layer.
# 4) The order of S, F has to be strictly followed
# 5) Example 'F1R1S3' means: 1x cube Flip, 1x (90deg) CW rotation of the 1st (Down) layer, 1x (90deg) CCW cube Spin
#
# For Rotations, the bottom servo makes a little extra rotation than target, before coming back to target; This
# is needed to recover the gaps between cube_hoder - cube - top_cover, and still getting a decent cube layers alignment.
#
#
# Developped on:
#  - Raspberry pi Zero 2 
#  - Raspberry Pi OS (Legacy) A port of Debian Buster with security updates and desktop environment
#    (Linux raspberry 5.10.103-v7+ #1529 SMP Tue 8 12:21:37 GMT 2022 armv71 GNU/Linux)
#
#############################################################################################################
"""



##################    imports standard libraries   #################################
import time                            # import time library
import RPi.GPIO as GPIO                # import RPi GPIO library
GPIO.setmode(GPIO.BCM)                 # setting GPIO pins as "Broadcom SOC channel" number, these are the numbers after "GPIO"
GPIO.setwarnings(False)                # setting GPIO to don't return allarms
from gpiozero import Servo, PWMLED     # import modules for the PWM part
# ##################################################################################



##################    GPIO pins for Servos and LED   ###############################
t_servo_pin = 12                # GPIO pin used for the top servo
b_servo_pin = 13                # GPIO pin used for the bottom servo
top_cover_led_pin = 18          # GPIO pin used to control the LED on/off
# ##################################################################################



##################    general servo_settings    ####################################
robot_init_status=False         # boolean to track the servos inititialization status
stop_servos=True                # boolean to stop the servos during solving proces: It is set true at the start, servos cannot operate
b_servo_operable=False          # variable to block/allow bottom servo operation
fun_status=False                # boolean to track the robot fun status, it is True after solving the cube :-)
s_debug=False                   # boolean to print out info when debugging
flip_to_close_one_step = False  # f_to_close steps (steps from flip up to close) is set false (=2 steps)
led_init_status = False
# ##################################################################################





def init_top_cover_led():
    global factory
    from gpiozero.pins.pigpio import PiGPIOFactory    # pigpio library is used, to use hardare timers on PWM (to avoid servo jitter)
    factory = PiGPIOFactory()                         # pin factory setting to use hardware timers, to avoid servo jitter
    
    # NOTE: High freq. on the led PWM prevents camera from seeing flickering
    top_cover_led = PWMLED(top_cover_led_pin,
                           active_high=True,
                           initial_value=0,
                           frequency=5000000,
                           pin_factory=factory)
    
    led_init_status = True
    return led_init_status, top_cover_led







def load_servos_parameters(print_out):
    """ Parameters are imported from a json file, to make easier to list/document/change the variables
        that are expected to vary on each robot.
        These servo_settings are under a function, instead of root, to don't be executed when this script is used from CLI
        with arguments; In this other case the aim is to help setting the servo to their mid position."""
    
    from Cubotino_T_settings_manager import settings as settings   # custom library managing the settings from<>to the settings files
    
    global t_servo, t_min_pulse_width, t_max_pulse_width, t_top_cover                       # top servo, pulse width, status
    global t_servo_close, t_servo_open, t_servo_read, t_servo_flip, t_servo_rel             # top servo related angles and status
    global t_flip_to_close_time, t_close_to_flip_time, t_flip_open_time, t_open_close_time, t_rel_time  # top servo timers
    
    global b_servo, b_min_pulse_width, b_max_pulse_width                                    # bottom servo and pulse width
    global b_servo_CCW, b_servo_CW, b_home, b_rel_CW, b_rel_CCW, b_extra_home_CW, b_extra_home_CCW   # bottom servo angles
    global b_servo_CCW_rel, b_servo_CW_rel, b_home_from_CCW, b_home_from_CW                 # bottom servo calculated angles
    global b_servo_home, b_servo_stopped, b_servo_CW_pos, b_servo_CCW_pos                   # bottom servo status
    global b_spin_time, b_rotate_time, b_rel_time                                           # bottom servo timers
    

    servo_settings = settings.get_servos_settings(reload=True)  # settings are retrieved from the settings Class

    if print_out:                                # case print_out variable is set true
        fname = settings.get_servo_settings_fname() # settings filename is retrieved
        print('\nImporting servos settings from the text file:', fname)    # feedback is printed to the terminal
        print('\nImported parameters: ')         # feedback is printed to the terminal
        for param, s in servo_settings.items():  # iteration over the settings dict
            print(f"{param}: {s}")               # feedback is printed to the terminal
        print()
          
    try:
        t_min_pulse_width = servo_settings['t_min_pulse_width']        # defines the min Pulse With the top servo reacts to
        t_max_pulse_width = servo_settings['t_max_pulse_width']        # defines the max Pulse With the top servo reacts to
        t_servo_close = servo_settings['t_servo_close']                # Top_cover close position, in gpiozero format
        t_servo_open = servo_settings['t_servo_open']                  # Top_cover open position, in gpiozero format
        t_servo_read = servo_settings['t_servo_read']                  # Top_cover camera read position, in gpiozero format
        t_servo_flip = servo_settings['t_servo_flip']                  # Top_cover flip position, in gpiozero format
        t_servo_rel_delta = servo_settings['t_servo_rel_delta']        # Top_cover release angle movement from the close position to release tension
        t_flip_to_close_time = servo_settings['t_flip_to_close_time']  # time for Top_cover from flip to close position
        t_close_to_flip_time = servo_settings['t_close_to_flip_time']  # time for Top_cover from close to flip position 
        t_flip_open_time = servo_settings['t_flip_open_time']          # time for Top_cover from open to flip position, and viceversa  
        t_open_close_time = servo_settings['t_open_close_time']        # time for Top_cover from open to close position, and viceversa
        t_rel_time = servo_settings['t_rel_time']                      # time for Top_cover to release tension from close position

        b_min_pulse_width = servo_settings['b_min_pulse_width']        # defines the min Pulse With the bottom servo reacts to
        b_max_pulse_width = servo_settings['b_max_pulse_width']        # defines the max Pulse With the bottom servo reacts to
        b_servo_CCW = servo_settings['b_servo_CCW']                    # Cube_holder max CCW angle position
        b_servo_CW = servo_settings['b_servo_CW']                      # Cube_holder max CW angle position
        b_home = servo_settings['b_home']                              # Cube_holder home angle position
        b_rel_CCW = servo_settings['b_rel_CCW']                        # Cube_holder release angle from CCW angle positions, to release tension
        b_rel_CW = servo_settings['b_rel_CW']                          # Cube_holder release angle from CW angle positions, to release tension
        b_extra_home_CW = servo_settings['b_extra_home_CW']            # Cube_holder release angle from home angle positions, to release tension
        b_extra_home_CCW = servo_settings['b_extra_home_CCW']          # Cube_holder release angle from home angle positions, to release tension
        b_spin_time = servo_settings['b_spin_time']                    # time for Cube_holder to spin 90 deg (cune not contrained)
        b_rotate_time = servo_settings['b_rotate_time']                # time for Cube_holder to rotate 90 deg (cube constrained)
        b_rel_time = servo_settings['b_rel_time']                      # time for Cube_holder to release tension at home, CCW and CW positions
        
        
    except:   # exception will be raised if json keys differs, or parameters cannot be converted to float
        print('Error on converting to float the imported parameters (at Cubotino_T_servos.py)')   # feedback is printed to the terminal                                  
        return robot_init_status                                        # return robot_init_status variable, that is False
    
    # bottom servo derived positions
    b_servo_CCW_rel = round(b_servo_CCW + b_rel_CCW,3)      # bottom servo position to rel tensions when fully CW
    b_servo_CW_rel = round(b_servo_CW - b_rel_CW,3)         # bottom servo position to rel tensions when fully CCW
    b_home_from_CW = round(b_home - b_extra_home_CW,3)      # bottom servo extra home position, when moving back from full CW
    b_home_from_CCW = round(b_home + b_extra_home_CCW,3)    # bottom servo extra home position, when moving back from full CCW
    
    # top servo derived position
    t_servo_rel = round(t_servo_close - t_servo_rel_delta,3) # top servo position to release tension
    
    timer = {}                                              # dict to store the servos timer values
    timer['t_flip_to_close_time'] = t_flip_to_close_time 
    timer['t_close_to_flip_time'] = t_close_to_flip_time
    timer['t_flip_open_time'] = t_flip_open_time
    timer['t_open_close_time'] = t_open_close_time
    if t_servo_rel < t_servo_close:                         # case the t_servo_rel_delta is > zero
        timer['t_rel_time'] = t_rel_time
    else:
        timer['t_rel_time'] = 0
    timer['b_spin_time'] = b_spin_time
    timer['b_rotate_time'] = b_rotate_time
    timer['b_rel_time'] = b_rel_time                                
    
    return timer   # return robot timers







def init_servo(print_out=s_debug, start_pos=0, f_to_close_mode=False, s_silent=False, init_display=True):
    """ Function to initialize the robot (servos position) and some global variables, do be called once, at the start."""
    
    global robot_init_status, fun_status, flip_to_close_one_step, led_init_status, top_cover_led
    global flip_to_close_one_step
    
    if init_display:
        set_display()
    
    if s_silent and not led_init_status:      # case s_silent is se True
        led_init_status, top_cover_led = init_top_cover_led()  # the GPIO for the led is initialized
        timer = load_servos_parameters(print_out)  # upload the servos parameters
        robot_init_status = True              # robot_init_status is set True
        return robot_init_status, timer       # the function returns initi status and timer
        
        
    if not led_init_status:                   # case the led_init_status variable is false
        led_init_status, top_cover_led = init_top_cover_led()  # the GPIO for the led is initialized
 
    
    if not robot_init_status and not s_silent:  # case the inititialization status of the servos false
        
        from Cubotino_T_pigpiod import pigpiod as pigpiod # start the pigpiod server
        
        if f_to_close_mode:                   # case the init got the f_to_close_mode as true
            flip_to_close_one_step = True     # flip_to_close_one_step is set true
        
        timer = load_servos_parameters(print_out)  # upload the servos parameters  
        if len(timer) == 0:                   # case the return is an empty dict
            print('Could not find Cubotino_T_servo_settings.txt')  # feedback is printed to the terminal                                  
            return robot_init_status          # return robot_init_status variable, that is False
        
        if start_pos==0:     # case the servos initial position equals zero (very first setting)
            t_servo = t_servo_create(t_min_pulse_width, t_max_pulse_width)  # t_servo servo object creation
            b_servo = b_servo_create(b_min_pulse_width, b_max_pulse_width)  # b_servo servo object creation                 
        else:                # case the servos initial position differes from zero
            t_servo = t_servo_create(t_min_pulse_width, t_max_pulse_width, t_servo_open)  # t_servo servo object creation
            b_servo = b_servo_create(b_min_pulse_width, b_max_pulse_width, b_home)        # b_servo servo object creation

        t_top_cover = start_pos               # variable to track the top cover/lifter position              
        b_servo_home=True                     # boolean of bottom servo at home
        b_servo_stopped = True                # boolean of bottom servo at location the lifter can be operated
        b_servo_CW_pos=False                  # boolean of bottom servo at full CW position
        b_servo_CCW_pos=False                 # boolean of bottom servo at full CCW position
        
        robot_init_status = True              # boolean to track the inititialization status of the servos is set true
        if print_out:                         # case the print_out variable is set true
            print("\nServo init done")        # feedback is printed to the terminal
        
        if start_pos !=0:                     # case the start_pos is not zero
            servo_start_pos(start_pos)        # servos are positioned to the start position    
        fun_status=False                      # boolean to track the robot fun status, it is True after solving the cube :-)
        cam_led_test()                        # makes a very short led test
        cam_led_Off()                         # forces the led off
        
        return robot_init_status, timer       # returns the init status and the timer(s) values
    
    else:                                     # caase robot_init_status already True
        return True                           # confirms the init status, and don't return the timer(s)







def t_servo_create(t_min_pulse_width, t_max_pulse_width, initial_pos=0):
    """top servo object creation."""
    global t_servo_pin, factory, t_servo
    
    try:                          # tentative
        t_servo                   # name of t_servo
        t_servo.close()           # t_servo object is eliminated
    except NameError:             # case a name error exception is raised
        pass
    
    t_servo = Servo(t_servo_pin,                                 # GPIO pin associated to the top servo
                    initial_value = initial_pos,                 # Top_cover positioned to initial_pos
                    min_pulse_width = t_min_pulse_width/1000,    # min Pulse Width the top servo reacts to
                    max_pulse_width = t_max_pulse_width/1000,    # max Pulse Width the top servo reacts to
                    frame_width=0.020,                           # min pulse width variation aceepted
                    pin_factory=factory)                         # way to use hardware based timers for the PWM
    
    time.sleep(0.7)          # time to let the servo reaching the initial_value angle
    return t_servo





def b_servo_create(b_min_pulse_width, b_max_pulse_width, initial_pos=0):
    """bottom servo object creation."""
    global b_servo_pin, factory, b_servo

    try:                          # tentative
        b_servo                   # name of b_servo
        b_servo.close()           # b_servo object is eliminated
    except NameError:             # case a name error exception is raised
        pass
    
    b_servo = Servo(b_servo_pin,                                # GPIO pin associated to the bottom servo
                    initial_value = initial_pos,                 # Cube_holder positioned to initial_pos
                    min_pulse_width = b_min_pulse_width/1000,    # min Pulse Width the bottom servo reacts to
                    max_pulse_width = b_max_pulse_width/1000,    # max Pulse Width the bottom servo reacts to
                    frame_width=0.020,                           # min pulse width variation aceepted
                    pin_factory=factory)                         # way to used hardware based timers for the PWM
    
    time.sleep(0.7)          # time to let the servo reaching the initial_value angle
    return b_servo







def set_display():
    global s_disp
    
    from Cubotino_T_display import display as s_disp    
    s_disp.set_backlight(0)     # display backlight is set off
    s_disp.show_cubotino()      # show cubotino logo on display, when this script is imported
    s_disp.set_backlight(1)     # activates the display backlight






def servo_tune_via_gui(debug, start_pos):
    
    global robot_init_status, stop_servos, b_servo_operable, s_debug
    
    robot_init_status=False        # boolean to track the servos inititialization status
    s_debug=debug                  # boolean to print out info when debugging
    robot_init_status = init_servo(s_debug, start_pos)
    stop_servos=False              # boolean to stop the servos during solving proces: It is set true at the start, servos cannot operate
    b_servo_operable=True          # variable to block/allow bottom servo operation
    return robot_init_status
    







def quit_func():
    """ Sets the used GPIO as output, and force them to low. This wants to prevent servos to move after closing the script."""
    
    GPIO.setup(top_cover_led_pin, GPIO.OUT, initial=GPIO.LOW)   # GPIO top_cover_led_pin (Top_cover_Led) is set as output, and force low
    GPIO.setup(t_servo_pin, GPIO.OUT, initial=GPIO.LOW)         # GPIO t_servo_pin (Top_cover servo) is set as output, and force low
    GPIO.setup(b_servo_pin, GPIO.OUT, initial=GPIO.LOW)         # GPIO b_servo_pin (Cube_holder servo) is set as output, and force low






def cam_led_On(value=0.05):
    """ Sets the top_cover led ON, with brightness in arg. Value ranges from 0 to 0.3"""
    
    if value >= 0.3:                              # case arg is bigger than, or equal to 0.3
        top_cover_led.value = 0.3                 # top cover led PWM is set to 30%
    else:                                         # case arg is smaller than 0.3
        top_cover_led.value = value               # top cover led PWM is set to arg value






def cam_led_Off():
    """ Sets the top_cover led OFF."""
    top_cover_led.off()      # top cover led PWM is set to 0






def cam_led_test():
    """ Fade the led On and Off at the init, to show the led worwing."""
    
    for i in range(0,32,4):            # iterates from 0 to 28 in steps of 4 
        top_cover_led.value = i/100    # top cover led PWM is set iterator %
        time.sleep(0.02)               # very short time sleep
    
    for i in range(28,-4,-4):          # iterates from 28 to 0 in steps of -4 
        top_cover_led.value = i/100    # top cover led PWM is set iterator %
        time.sleep(0.02)               # very short time sleep
    
    top_cover_led.off()                # top cover led PWM is set to 0
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

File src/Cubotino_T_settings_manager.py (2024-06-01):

#!/usr/bin/python
# coding: utf-8

"""
#############################################################################################################
#  Andrea Favero 31 May 2024
#
# This script relates to CUBOTino Autonomous, a small and simple Rubik's cube solver robot 3D printed
# This specific script manages the interactions with the settings files (json text files).
#
# Parameters at the settings files are those more likely to vary between differentt robots.
# Having the setting "insulated" in text files makes easier to list, document, change them.
#
# Mac address is used to match boards and settings on my robots: This limits mistakes at my end. 
#
#############################################################################################################
"""

import sys, glob, os.path, pathlib, json
from getmac import get_mac_address           # library to get the device MAC ddress


class Settings:

    def __init__(self):
        """Check if local settings exist, if not are created.
            Reads the local settings files.
            Parameters and settings are imported.
            Settings datatypes are parsed."""
        
        # mac address is used by myself (Andrea Favero), to upload the settings fitting my robot
        self.folder = pathlib.Path().resolve()            # active folder (should be home/pi/cubotino/src)
        self.macs_AF = self.get_macs_AF(self.folder)      # mac addresses of AF bots are retrieved
        self.eth_mac = get_mac_address().lower()          # mac address of the Pi board is retrieved
        self.check_local_settings()                       # checks whether local settings files exist
        self.load_settings()                              # loads settings




    def load_settings(self):
        """Calls the function to read and parse the settings."""
        
        s = self.read_settings()                          # reads the general robot settings
        servos_s = self.read_servos_settings()            # reads the servos settings
        
        self.s = self.parse_settings(s)                        # converts settings to correct datatype
        self.servos_s = self.parse_servos_settings(servos_s)   # converts servos settings to correct datatype




    def get_macs_AF(self, folder):
        """Returns a tuple with the mac adresses from a text file (macs_AF.txt)."""
        
        fname = os.path.join(folder,'macs_AF.txt')        # filename for the text file with listed the mac adrresses
        macs_AF = []                                      # emppty list to store the mac addresses
        if os.path.exists(fname):                         # case the servo_settings file exists
            with open(fname, "r") as f:                   # file is opened in reading mode
                macs = f.readlines()                      # text lines are retrieved
                for mac in macs:                          # iteration over the lines
                    macs_AF.append(mac.lower().strip())   # stripped lines contents are appended to the mac list
        
        # in case the file is missed the returned tuple is empty
        return tuple(macs_AF)                             # list is converted to tuple and returned




    def get_fname_AF(self, fname, pos):
        """Generate settings filenames for AF robot."""
        return fname[:-4] + '_AF' + str(pos+1) + '.txt'




    def check_local_settings(self):
        """Check the presence of local settings, If not present, the default settings files
            are copied as local settings files."""
        
        fnames_default = ('Cubotino_T_settings_default.txt' , 'Cubotino_T_servo_settings_default.txt')
        fnames_local = ('Cubotino_T_settings.txt', 'Cubotino_T_servo_settings.txt')
        
        for i in range(2):
            fname = fnames_local[i]                               # file name to locally save general settings
            
            if self.eth_mac in self.macs_AF:                      # case the script is running on AF (Andrea Favero) robot
                pos = self.macs_AF.index(self.eth_mac)            # mac address row position in macs_AF.txt file
                fname = self.get_fname_AF(fname, pos)             # AF robot settings file name
            else:                                                 # case the script is not running on AF (Andrea Favero) robot
                fname = os.path.join(self.folder,fname)           # folder and file name for the settings, to be tuned
            
            if not os.path.exists(fname):                         # case the local settings file does not exist
                fname_d = os.path.join(self.folder,fnames_default[i]) # folder and file name for the settings, to be tuned
                
                if not os.path.exists(fname_d):                   # case the default settings file does not exist
                    print("\n\n\n")                               # print empty lines
                    print("#"*86)                                 # print a separation line
                    print(f"Missed file {fnames_default[0]}  or  {fnames_default[1]}") # feedback is printed to the terminal
                    print("Double check the wastebacket if these files were erared by mistake.") # feedback is printed to the terminal
                    print("These files are anyhow available at GitHub project page") # feedback is printed to the terminal
                    print("#"*86, "\n\n\n")                       # print a separation line
                    sys.exit(1)                                   # script is quitted with error
                
                with open(fname_d, 'r') as input:                 # default settings file is opened as input
                    output = open(fname, 'w')                     # local settings file is opened to be written
                    output.write(input.read())                    # default settings are saved into the local settings file
                
                print(f"One time action: Creating local settings file {fname}")  # feedback is printed to the terminal





    def get_settings(self):
        """Returns the general robot settings dict."""
        return self.s





    def get_servos_settings(self, reload=False):
        """Returns the servos settings dict."""
        if reload:
            self.load_settings()
        return self.servos_s
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

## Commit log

2024-01-26 I made a mess
    [Alternative_Servo_axis_inf.stl, Alternative_Servo_axis_inf.stp, Alternative_Servo_axis_sup.stl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]
2024-02-10 Solved bug on FCS
    Made more robust the fcs uploading when the file has empty lines.
    [Cubotino_T_servos_GUI.py]
2024-02-22 Fix case where percent = 0 causes x2 < x1 in the draw rectangle. (#17)
    [Cubotino_T_display.py]
2024-03-10 Improved settings management
    Local settings won't get overwritten by git pull.
    Rationalized settings management, via a dedicated Class in Cubotino_T_settings_manager.py
    [Cubotino_T_camera_os10.py, Cubotino_T_camera_os11.py, Cubotino_T_display.py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]
2024-03-14 Solved bug from previous commit
    Changes on sliders weren't saved to Cubotino_T_servo_settings.txt
    [Cubotino_T_servos_GUI.py]
2024-03-14 Solved bug from previous commit
    Preventing older characteres at file-end, when saving less content in *settings.txt
    [Cubotino_T_settings_manager.py]
2024-03-15 Add support for ST7735 and ST7789 display boards (#19)
    * Add support for mulitple displays,
    ST7735 is default
    ST7789 is supported.
    * Adjust font scaling for ST7789, font sizes better match the ST7735.
2024-03-17 Add PCB covers for waveshare displays (#23)
    Information is very clear, the interested Makers will download the zip file
2024-03-18 Remove broken and uneeded imports (#24)
    [Cubotino_T_camera_os10.py, Cubotino_T_camera_os11.py]
2024-03-18 Fixed bug at GUI
    Preventing old characters to be saved at Json files when newer content has less characters to be saved.
    [Cubotino_T_settings_manager.py]
2024-04-01 Speed Optimize: Allow 180 degree spins and rotates (#26)
    * Add moves dictionary from Home/CW/CCW
    * Add 180degree rotations
    * Optimize Moves: Spins more efficient that flips
    Cleanup Comments
    [Cubotino_T_moves.py, Cubotino_T_servos.py]
2024-04-10 Effective opt2 on 180deg
    Adapted opt2 for 180deg rotations
    Removed a bug at opt2 when less than 2 moves
    Spin to home at moves end (Cubotino_T_moves.py)
    Adapted animations (Cubotino_T.py and (Cubotino_T_test-random.py)
    [Cubotino_T_moves.py]
2024-06-01 Add Dominant colours analysis
    Dominant colour analysis added (-D or --dominant argument).
    Improved PiCamera V2 settings and prepared for V3 (4 lines of code to be uncommented).
    PiCamera_holder (stl and stp) compatibilie with PiCamera V1, V2 and V3.
    Updated Instructions (V7.4) for more info.
    [PiCamera_holder.stp, PiCamera_holder_V1_V2_V3.stl, PiCamera_holder_V1_V2_V3.stp]
2024-06-02 Add Dominant colours analysis
    Rev 7.5: Fixed a bug when OS11 and V1.3 camera with old s_mode setting (s_mode needs to be 1 and not 7).
    [Cubotino_T_camera_os11.py]
